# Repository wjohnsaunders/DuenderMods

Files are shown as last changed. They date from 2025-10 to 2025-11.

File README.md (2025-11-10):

# Modified files for Duender MGN9 Version

I wanted to use the updated MGN9 files for constructing my Duender. This
was because a number of improvements had been made to the design. Also I
I would like to install rails in the future without needing to reprint all
of the parts. The MGN9 has improved stacking of the flanged bearing using
0.5mm washers instead of printer shims.

I also saw the "Top Motor Mount w/ Double Shear for Duender" from Andizzle
on Printables, and liked how rigidly it mounted to the frame. However this
mount was not suitable for the MGN9 version.

These files are not re-mixes of the original STEP or STL files. I have
designed each one from scratch in FreeCAD using just the dimensions of
the original parts to make them work in place of the originals. However
I deem them a remix as they are intended for the Duender, and replace
the original parts in a like-for-like way.

I want to thank Sergei Irbis for the design of the Duender and providing
a means for my Ender 3 to continue as a useful 3D printer.

I also want to thank Andizzle for the improved motor mounts that I have
based my motor mounts design on.

## Front Tensions MGN9

This project contains a re-design of the front tensioner housings from
Sergei Irbis, and they re-use the stock pulley holder inserts.

The main change is that it uses the M5x45 and M5x25 bolts from the Ender
3 (you need to tap your threads into the extrusion at least 20mm) to make
for a very strong connection.

I have also adjusted the geometry to provide a solid end-stop for my newly
designed Wheel to MGN9 Adapters.

Finally I played with the asthetic to get something that I like better.

## Motor Mounts MGN9

This project contains a re-design of the motor mounts from Andizzle, however
adds 8mm to the deck height to make them compatible with the MGN9 project.

I also removed the trianguler mount from the bottom, as in the future I will
have a 20x40 extrusion there to support a 3rd heated bed mount. It seems
plenty strong enough without it.

Finally it uses the M5x45 bolts from the Ender 3 (you need to tap your
threads into the extrusion at least 20mm) to mount into the 2040 Y-axis
extrusions to make for a very strong connection.

You need to mount both of the motor mounts to 2020 extrusion first, as the
M5x45 bolts prevent access to the bolts that go into the end of the 2020
extrusion. Then you use the M5x45 bolts to mount the assembly to the frame.

Note that this redesign moves the bolt positions somewhat, so that you cannot
mix and match the top and bottom parts from Andizzles project. The belt path
remains compatible so there should not be any effect on kinematics.

## Wheel To MGN9 Adapter

This is the mod I first started working on. I was looking for options not
to have to buy a sheet of aluminium then drill and cut the plates. I used
purchased open-build plates for the Z axis, but this doesn't work for the
X gantry.

I noticed that the V-wheels posiion the plate approximately 4mm above the
top of the extrusion, where as an MGN9 carriage positions it 10mm above
the extrusion. It is known that the aluminium plates cannot be 3D printed
because 3mm thickness is not rigid enough.

So I thought that if I 3D printed a 6mm plate that should increase rigitity
and bring the alignment in line with an MGN9 carriage. So I decided I
would design a 6mm adapter than would look like an MGN9 carriage for the
stock parts to mount onto.

I have done a few revisions of this in order to move the inner wheel out of
the way of potential toolheads. I also had to move the rear outer wheel back
to provide stability against twisting. I believe it works well as a stop-gap
until you can install rails. The only negative is that you cannot adjust the
wheel tension without removing the stock parts from the top. So make sure
you adjust the wheel tension before full assembly.

## X Mount MGN12

This mod adds support for using an MGN12H linear rail and carriage for the X
axis.

I feel that these size rails mount better on the V-slot extrusions, and MGN12
is the current X axis standard for DIY printers like the Vorons and others.
It opens up more options for alternative toolheads and mounting systems. The
only con being that the nozzle is pushed further forward.

## EMS Panel and Various EMS Mounts

What is EMS? It is a system for managing the electronics for 3D printers from
FizzyTechs. It consists of a panel with hexagon cutouts, a set of hexagon
shaped plugs that fit into the panel, and a repository of mounts for various
3D printer electrical components. The idea is that if you replace a component,
or need to move one around, you can just print the mount for the new component,
or move the plugs to a different cutout. There are also plugs for zip-ties,
and a set of cable ducts for solving any cable management issue.

https://www.printables.com/model/558357-ft-ems-mounts-repository

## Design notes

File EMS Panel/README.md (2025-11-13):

# EMS Panel

This is an EMS panel for the Duender 3D printer. There is a version with
6 tabs and 8 tabs. The 8 tab option is useful if the Z steppers are
towards the middle, while the 8 tab option is better if the steppers are
further forward.

What is EMS? It is a system for managing the electronics for 3D printers
from FizzyTechs. It consists of a panel with hexagon cutouts, a set of
hexagon shaped plugs that fit into the panel, and a repository of mounts
for various 3D printer electrical components. The idea is that if you
replace a component, or need to move one around, you can just print the
mount for the new component, or move the plugs to a different cutout.
There are also plugs for zip-ties, and a set of cable ducts for solving
any cable management issue.

https://www.printables.com/model/558357-ft-ems-mounts-repository

Note that there is no upper lid for the electronics bay, I was thinking a sheet
of Acrylic with a cutout or two for fans. The hexagon holes in the EMS panel
will allow cooling air to pass out from underneath the Duender.

## Printing

Print with the flat side down, it should import in the correct orientation.
No supports are necessary. There are some bridges, but they should print OK
provided you have some part cooling enabled.

The model is 288x249 so you will need a printer capable of 300mm. You can
use the slicer to split it into 4 parts, then super glue it back together.
There are “dog-bone” joiners available for EMS if gluing is not strong enough.

The dimensions should give you 0.5mm gap all around, however filament
shrinkage could cause more gap. So it's best to calibrate the shrinkage for
your filament and set that in the slicer before printing.

## Installation

The panel mounts in the bottom of the rectangle formed by the 4040 extrusions
in the base of the Duender. Your electronics mounts to the base using the plugs
and adapter mounts from the FT EMS repository. I suggest working out the
electronics component placement while the EMS base is not installed, as it will
be easier to make adjustments. Once you have worked out the positions, remove
the components from the mounts, install the panel and re-install the components.

Use 8/6 sets of M5x8 bolt and M8 T-nut (should have a bunch available from the
corner braket packs) to bolt it to the upper V-slot. The EMS base should be
flush with the bottom of the 4040 extrusions, and should clear the Z-axis
steppers if you didn't use spacers to place them lower.

## CAD

The part is designed using FreeCAD.

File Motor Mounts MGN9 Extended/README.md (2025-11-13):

# Motor Mounts MGN9 Extended

This project takes my previous MGN9 Motor Mounts project and moves everything
further back to allow more Y axis travel. You will probably want to have 320mm
rails (get 350mm rails and trim 30mm from it with an Inox cutting wheel on an
angle grinder) with these mounts to give 280mm of Y travel (45mm outside the
print bed area).

Also the top half is relocated a further 10mm back, as I was having a problem
with the toolhead PCB (one that mounts to the extruder stepper) hitting the
top mounted stepper motors. The top half of the mounts are the same as my
previous mounts, so no need to reprint if you already have them.

Also note that you will need longer belts as a consequence of moving
everything back. Belt alignment stays the same, just the run from front to
back is longer.

You need to mount both of the motor mounts to 2020 extrusion first, as the
M5x45 (or M5x40) bolts prevent access to the bolts that go into the end of
the 2020 extrusion. Then you use the M5x45/40 bolts (4 instead of 2 in this
version) to mount the assembly to the frame.

## Printing

Print with the flat side down, it should import in the correct orientation.
The parts are designed such that no supports are required to print. I suggest
4 walls, 5 top and bottom layers, and 40% infill for strength as this part is
under tension from the belts. This is the standard Voron printing specs.

## Installation

You will need an M8 tap to cut a thread into the largest hole. This should
be easy as it is just plastic. I will try and figure out how to design a
thread so it gets 3D printed in a future revision.

Next you need 5 heat-set inserts per mount, M3x5x4, which go into the 5
middle sized holes. The circular end of the insert should fit into the
hole, then push it all the way in with a soldering iron.

Note: In order to get the insert properly aligned, I push it almost in,
then flip the part over and press down hard on a flat heat resistance
surface (I use a small sheet of aluminum on my desk). The remaining heat
allows the insert to go all the way in, and the flat surface ensures the
insert is properly aligned when the plastic sets hard.

Move your bearing stacks from the existing top cover to the new top cover.

Mount the top cover to the bottom part. The existing bolts should be OK,
6 x M3x30 and 1 x M8x35 (from Ender 3 Y-axis tensioner).

You will likely need to tap a longer M5 threads into the end of your Y
extrusions. I have designed for the M5x45 bolts to have 19mm of thread
protruding from the mount, so I suggest extending the thread length to
20mm with a tap. Or use the M5x40 bolts with a 15mm tapped hole. Make
sure to use the original thread to guide the tap in, as you don't want
it cutting a new thread that is out of alignment. Make sure to tap both
the top and bottom holes.

You will also need to tap a thread into the 2020 extrusion, the length
of the thread depends on the bolt length you use, but use a button head
bolt as there is no clearance for anything else. I would suggest an
M5x12 as a minimum, and an M5x16 is even better.

You then mount both of the motor mounts to 2020 extrusion first. Start
with a T-nut and M5x8 from the back of the mount, don't fully tighten.
Next install the M5x12/16 into the end of the 2020 extrusion, tighten
this first then go back and tighten the M5x8. Repeat for the motor
mount on the other side of the extrusion.

Finally use the M5x45/40 bolts to mount the rear-motor mount assembly
onto the frame. You might find that you need to flex the frame, if it
is slightly out of alignment, so that the bolts go in.

The rear of the frame should now be very rigid, and you should look at
adding a brace to the front of the frame to provide similar rigidity.

## CAD

The part is designed using FreeCAD.

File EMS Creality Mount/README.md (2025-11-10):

# EMS Creality Mount

This is an EMS mount for the Creality control boards as used in the older
Ender-3 and CR-10s.

What is EMS? It is a system for managing the electronics for 3D printers from
FizzyTechs. It consists of a panel with hexagon cutouts, a set of hexagon
shaped plugs that fit into the panel, and a repository of mounts for various
3D printer electrical components. The idea is that if you replace a component,
or need to move one around, you can just print the mount for the new component,
or move the plugs to a different cutout. There are also plugs for zip-ties,
and a set of cable ducts for solving any cable management issue.

https://www.printables.com/model/558357-ft-ems-mounts-repository

## Printing

Print with the flat side down, it should import in the correct orientation.
The part has been designed to print with no supports.

## Installation

Install 5 heatset inserts from the top. Attach the mount with some EMS plugs
into the base. Attach the Creality control board to the mount with some
M3x6 or M3x8 bolts.

## CAD

The part was designed using FreeCAD.

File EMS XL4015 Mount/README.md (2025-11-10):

# EMS XL4015 Mount

This is an EMS mount for the XL4015 voltage regular that is often used to
power Rasoberry Pis from a 3D printers 24V PSU.

What is EMS? It is a system for managing the electronics for 3D printers from
FizzyTechs. It consists of a panel with hexagon cutouts, a set of hexagon
shaped plugs that fit into the panel, and a repository of mounts for various
3D printer electrical components. The idea is that if you replace a component,
or need to move one around, you can just print the mount for the new component,
or move the plugs to a different cutout. There are also plugs for zip-ties,
and a set of cable ducts for solving any cable management issue.

https://www.printables.com/model/558357-ft-ems-mounts-repository

## Printing

Print with the flat side down, it should import in the correct orientation.
The part has been designed to print with no supports.

## Installation

Install 2 heatset inserts from the top. Attach the mount with an EMS plug or
two. Attach the XL4016 to the mount with some M3x6 or M3x8 bolts.

## CAD

The part was designed using FreeCAD.

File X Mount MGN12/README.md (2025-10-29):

# X Mount MGN12

This mod is for Duender MGN9, however it confusingly supports an MGN12 rail
on the X axis. Doing this expands the toolhead options as effectively any
Voron toolhead will simply fit as-is. I have a StealthBurner on mine, and
I used the Voron X Carriage STLs to mount it. However XOL, A4T, Archetype,
DragonBurner, etc will all simply bolt on. I would also like to experiment
with a StealthChanger for multiple heads in the future, and this mod
enables that. Some toolheads still support MGN9, but it is not as many as
supports MGN12.

Essentially all this mod does is move the idler pulley positions 3mm forward
to cater for the extra height in the MGN12 rail. I also fiddled with the
cutouts on the top to make it easy to get an allen wrench onto the bolt
underneath. This was a re-design in FreeCAD rather than an STL remix.

## Printing

Print with the flat side down, it should import in the correct orientation.
No supports are necessary. There are builtin bridges for the recessed holes,
so I suggest using a part cooling fan by the 3rd layer or so.

## Installation

After printing, install heat-set inserts in the left and right lower parts.

You will need 10 heat-set inserts in total, M3x5x4, installed as per the
original part. The circular end on the insert should fit into the hole, then
push it all the way in with a soldering iron. I recommend that they be
installed from bottom, as that provides a stronger connection. Note that for
the hole with the 10mm column, they can only go in from the bottom.

Note: In order to get the insert properly aligned, I push it almost in,
then flip the part over and press down hard on a flat heat resistance
surface. The remaining heat allows the insert to go all the way in, and
the flat surface ensures the insert is properly aligned and flush.

You will also need 10 x M3x30 bolts in total, along with bearings and shims.
All of the standard Duender MGN9 hardware fits in the equivalent locations.

Note: Shim stacks. In order to match the Voron belt spacing (4mm between the
inner edges of the belts) I have altered my bearing and shim stacks.
- On the stacks that have 2 bearing sets (the rear motor mounts) I use 1.5mm
of shims on the outside and 2mm of shims in the middle, and I don't use a shim
between the bearing halves because I don't want the belts moving up and down.
- On the stacks with a single bearing set, I use 1.5mm of shims on both sides.
Again no shims between the bearing halves.

## CAD

The part is designed using FreeCAD. I can't provide STEP files, sorry, as
FreeCAD can only import STEP files, it cannot export them as far as I know.

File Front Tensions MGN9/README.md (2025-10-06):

# Front Tensions MGN9

This project contains a re-design of the front tensioner housings from
Sergei Irbis, and they re-use the stock pulley holder inserts.

The main change is that it uses the M5x45 and M5x25 bolts from the Ender
3 (you need to tap your threads into the extrusion at least 20mm) to make
for a very strong connection.

I have also adjusted the geometry to provide a solid end-stop for my newly
designed Wheel to MGN9 Adapters.

Finally I played with the asthetic to get something that I like better.

## Printing

Print in the same orientation as the stock parts, it should import in the
correct orientation. No support is required as hole recesses have support
built into the model.

## Installation

These should pretty much be a swap from the original part, you re-use the
existing pulley holders so no rebuilding of the bearing stack.

However you will likely need to tap a longer M5 thread into the end of
your extrusions. I have designed for the M5x45 and M5x25 bolts to have
18mm of thread protruding from the mount, so I suggest extending the
thread length to 20mm with a tap.

Use some tape on the tap to make the 20mm position. Make sure to use the
original thread to guide the tap in, as you don't want it cutting a new
thread that is out of alignment.

## CAD

The part is designed using FreeCAD. I can't provide STEP files, sorry, as
FreeCAD can only import STEP files, it cannot export them as far as I know.

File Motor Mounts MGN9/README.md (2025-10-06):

# Motor Mounts MGN9

This project contains a re-design of the motor mounts from Andizzle, however
adds 8mm to the deck height to make them compatible with the MGN9 project.

I also removed the trianguler mount from the bottom, as in the future I will
have a 20x40 extrusion there to support a 3rd heated bed mount. It seems
plenty strong enough without it.

Finally it uses the M5x45 bolts from the Ender 3 (you need to tap your
threads into the extrusion at least 20mm) to mount into the 2040 Y-axis
extrusions to make for a very strong connection.

You need to mount both of the motor mounts to 2020 extrusion first, as the
M5x45 bolts prevent access to the bolts that go into the end of the 2020
extrusion. Then you use the M5x45 bolts to mount the assembly to the frame.

Note that this redesign moves the bolt positions somewhat, so that you cannot
mix and match the top and bottom parts from Andizzles project. The belt path
remains compatible so there should not be any effect on kinematics.

## Printing

Print with the flat side down, it should import in the correct orientation.
In order for the flange bearing recess to print correctlty, enable manual
supports, and paint the circular flange bearing recess in the slicer, and
when sliced check that support is generated just in that area.

I hope to produce a file with support designed in, but for now you will have
to use manual support and paint it on. Automatic support will work, however
it will fill the holes intended for the heatset inserts, and they are a
pain to remove.

## Installation

You will need an M8 tap to cut a thread into the largest hole. This should
be easy as it is just plastic. I will try and figure out how to design a
thread so it gets 3D printed in a future revision.

Next you need 5 heatset inserts per mount, M3x5x4, which go into the 5
middle sized holes. The circular end on the insert should fit into the
hole, then push it all the way in with a soldering iron.

Note: In order to get the insert properly aligned, I push it almost in,
then flip the part over and press down hard on a flat heat resistance
surface. The remaining heat alows the insert to go all the way in, and
the flat surface ensures the insert is properly aligned.

Move your bearing stacks from the existing top cover to the new top cover.

Mount the top cover to the bottom part. The existing bolts should be OK,
6 x M3x30 and 1 x M8x35 (from Ender 3 Y-axis tensioner).

You will likely need to tap a longer M5 thread into the end of your Y
extrusions. I have designed for the M5x45 bolts to have 18mm of thread
protruding from the mount, so I suggest extending the thread length to
20mm with a tap.

Use some tape on the tap to make the 20mm position. Make sure to use the
original thread to guide the tap in, as you don't want it cutting a new
thread that is out of alignment.

You will also need to tap a thread into the 2020 extrusion, the length
of the thread depends on the bolt length you use, but use a button head
bolt as there is no clearance for anything else. I would suggest an
M5x16 as a minimum to provide a strong connection.

You then mount both of the motor mounts to 2020 extrusion first. Start
with a T-nut and M5x8 from the back of the mount, don't fully tighten.
Next install the M5x16 into the end of the 2020 extrusion, tighten this
first then go back and tighten the M5x8. Repeat for the other motor
mount on the other side of the extrusion.

Finally use the M5x45 bolts to mount the rear-motor mount assembly onto
the frame. You might find that you need to flex the frame to line up
the bolts so that they go in.

The rear of the frame should now be very rigid, and you should look at
adding a brace to the front of the frame to provide similar rigitity.

## CAD

The part is designed using FreeCAD. I can't provide STEP files, sorry, as
FreeCAD can only import STEP files, it cannot export them as far as I know.

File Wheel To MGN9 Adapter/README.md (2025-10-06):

# Wheel To MGN9 Adapter

This is the mod I first started working on. I was looking for options not
to have to buy a sheet of aluminium then drill and cut the plates. I used
purchased open-build plates for the Z axis, but this doesn't work for the
X gantry.

I noticed that the V-wheels posiion the plate approximately 4mm above the
top of the extrusion, where as an MGN9 carriage positions it 10mm above
the extrusion. It is known that the aluminium plates cannot be 3D printed
because 3mm thickness is not rigid enough.

So I thought that if I 3D printed a 6mm plate that should increase rigitity
and bring the alignment in line with an MGN9 carriage. So I decided I
would design a 6mm adapter than would look like an MGN9 carriage for the
stock parts to mount onto.

I have done a few revisions of this in order to move the inner wheel out of
the way of potential toolheads. I also had to move the rear outer wheel back
to provide stability against twisting. I believe it works well as a stop-gap
until you can install rails. The only negative is that you cannot adjust the
wheel tension without removing the stock parts from the top. So make sure
you adjust the wheel tension before full assembly.

## Printing

Print with the flat side down, it should import in the correct orientation.
No supports are necessary.

## Installation

Install the heatset inserts before the wheels.

You will need 4 heatset inserts per adapter, M3x5x4, which go into the 4
inner holes. The circular end on the insert should fit into the hole, then
push it all the way in with a soldering iron. They can be installed from
either the top or bottom, but provide a stronger connection if they are
installed from underneath. You will need either M3x10 or M3x12 bolts to
attach the X axis parts to the adapter.

Note: In order to get the insert properly aligned, I push it almost in,
then flip the part over and press down hard on a flat heat resistance
surface. The remaining heat alows the insert to go all the way in, and
the flat surface ensures the insert is properly aligned.

Obtain 2 fixed position V-wheel assemblies, and 1 adjustable V-wheel assembly
from your box of Ender 3 parts (I used parts from the Z-axis).

The fixed wheels go on the outside, and the adjustable wheel on the inside.
Install a bolt, the bolt head should sit in the recess so that the top of
the adapter is flat. Put on either a spacer or the adjuster cam, then a
wheel and finally a bolt.

The fixed wheels can be tightened. Keep the adjustable wheel loose. Install
on the extrusion, adjust the cam until there is no slop, an you can still
turn the wheels with your fingers. The adapter should easilt slide back
and forth on the extrusion. Remove the adapter and do a final tighten.

They are now ready to install the stock X axis parts on top.

## CAD

The part is designed using FreeCAD. I can't provide STEP files, sorry, as
FreeCAD can only import STEP files, it cannot export them as far as I know.

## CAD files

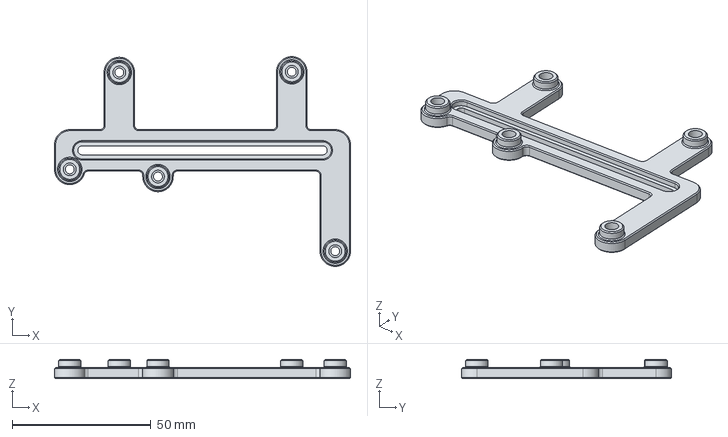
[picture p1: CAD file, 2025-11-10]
EMS Creality Mount/CAD/EMS Creality Mount.STEP
106.7 x 75.6 x 7.00 mm

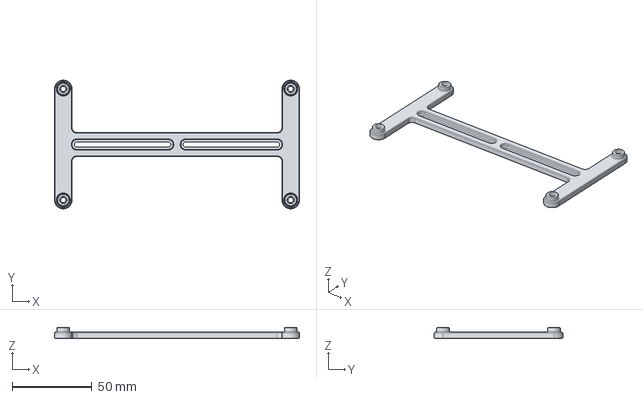
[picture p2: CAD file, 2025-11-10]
EMS Fysetc Spider Mount/CAD/EMS Fysetc Spider Mount.STEP
153.3 x 80.5 x 7.00 mm

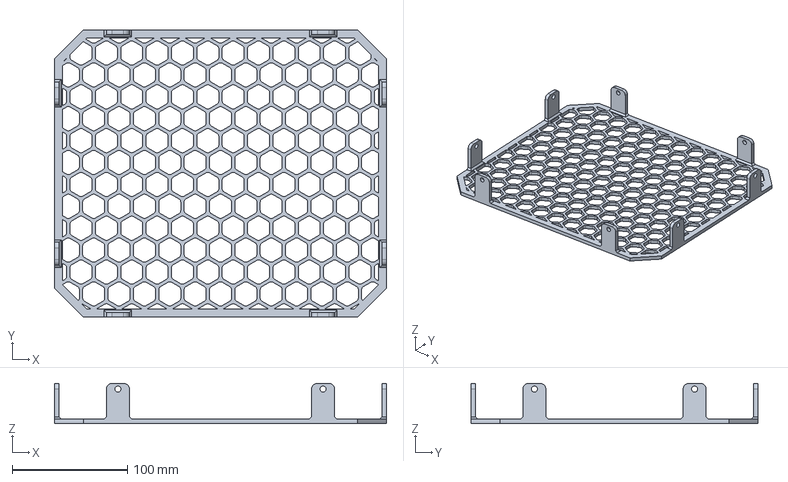
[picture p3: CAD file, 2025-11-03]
EMS Panel/CAD/EMS_Bottom.FCStd
288.0 x 249.0 x 35.0 mm

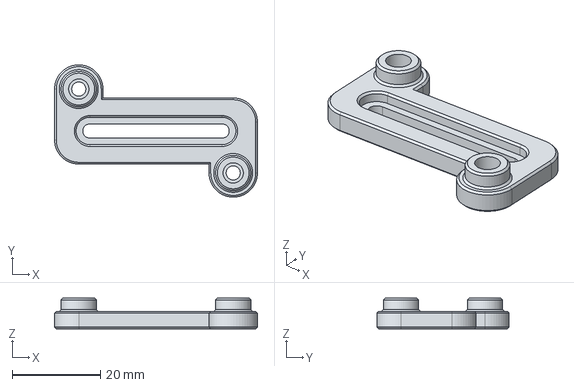
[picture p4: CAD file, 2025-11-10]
EMS XL4015 Mount/CAD/EMS XL4015 Mount.STEP
46.0 x 30.0 x 7.00 mm

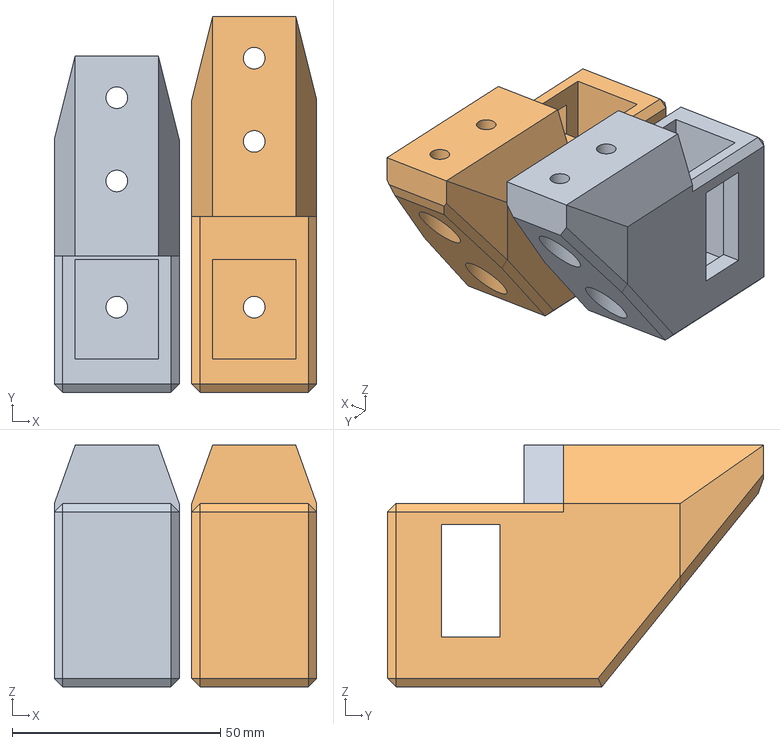
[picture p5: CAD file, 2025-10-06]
Front Tensions MGN9/CAD/FrontBeltTensioner.FCStd
63.0 x 90.3 x 58.0 mm
Left
Right

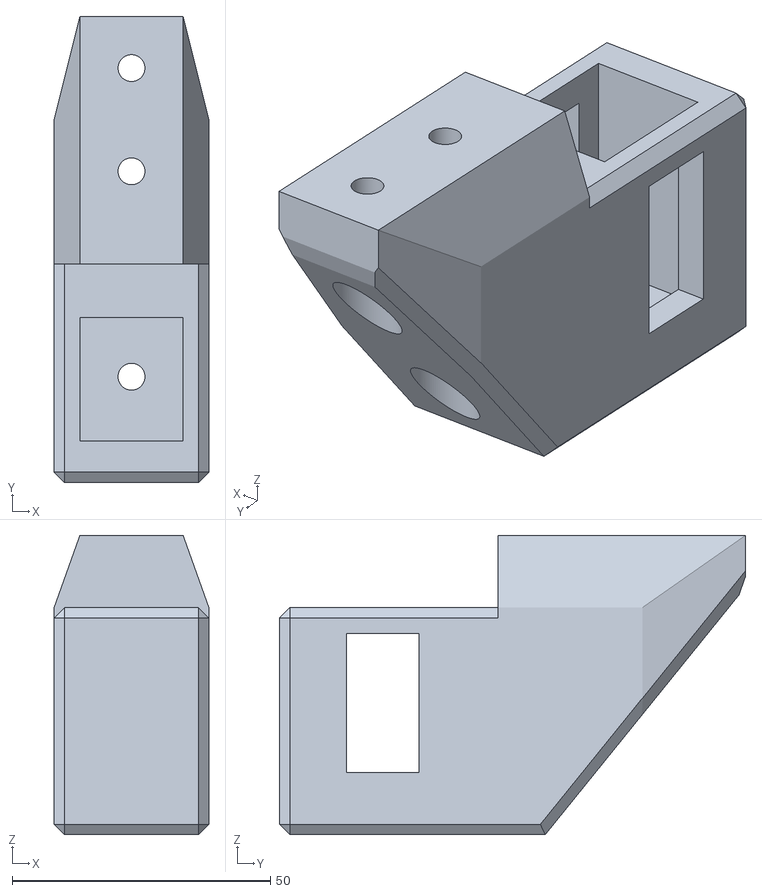
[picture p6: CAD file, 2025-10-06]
Front Tensions MGN9/STL/FrontBeltTensioner-Right.stl
30.0 x 90.3 x 58.0

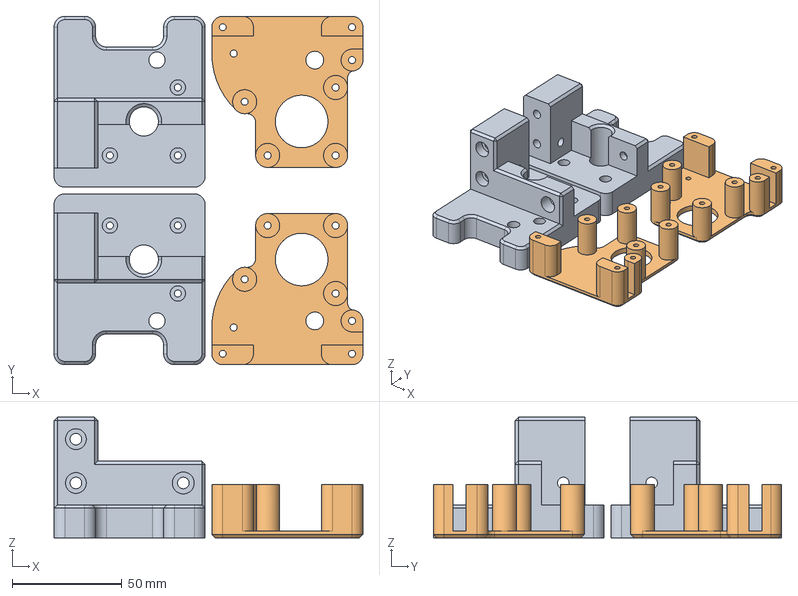
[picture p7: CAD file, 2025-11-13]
Motor Mounts MGN9 Extended/CAD/MotorMountMGN9Extended.step
141.0 x 159.0 x 55.0 mm
BottomRight
BottomLeft
TopRight
TopLeft

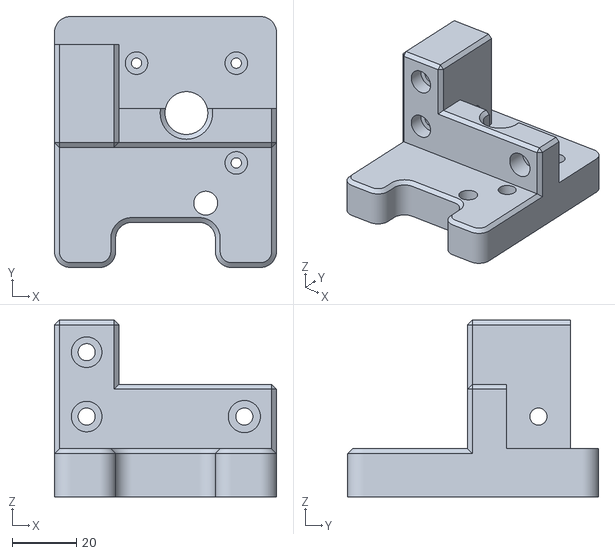
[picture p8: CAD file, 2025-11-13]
Motor Mounts MGN9 Extended/STL/MotorMountMGN9Extended-BottomLeft.stl
69.0 x 78.0 x 55.0

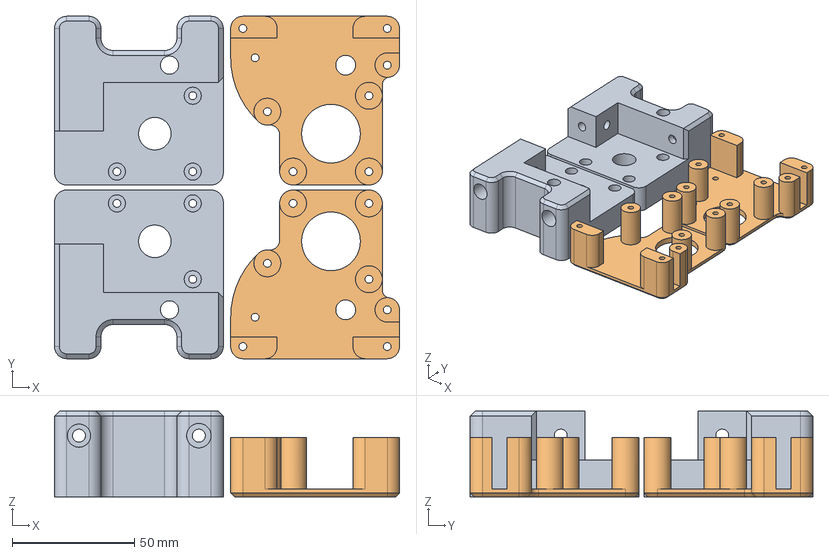
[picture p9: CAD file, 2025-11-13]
Motor Mounts MGN9/CAD/MotorMountMGN9.step
141.0 x 140.0 x 35.0 mm
BottomRight
BottomLeft
TopRight
TopLeft

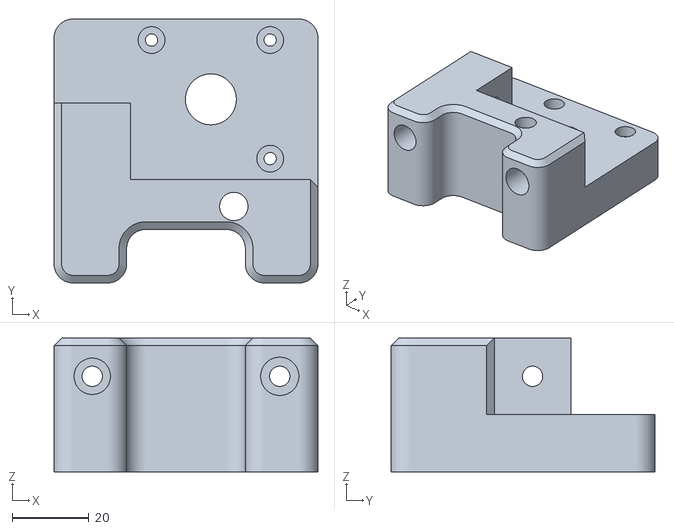
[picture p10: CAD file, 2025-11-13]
Motor Mounts MGN9/STL/MotorMountMGN9-BottomLeft.stl
69.0 x 69.0 x 35.0

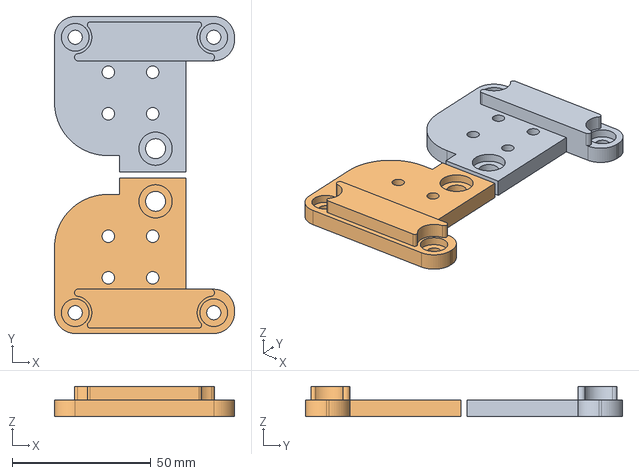
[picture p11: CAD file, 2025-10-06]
Wheel To MGN9 Adapter/CAD/WheelToMGN9Adapter.FCStd
65.0 x 114.4 x 11.0 mm
Left
Right

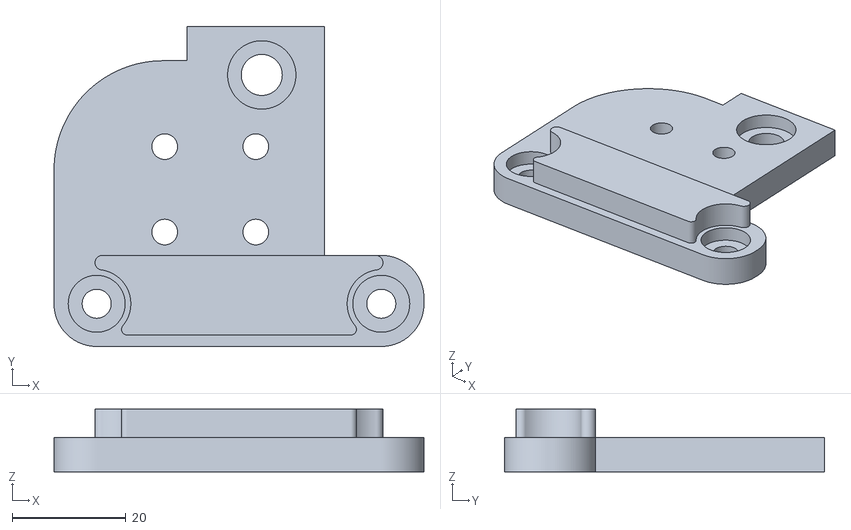
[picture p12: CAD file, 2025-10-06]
Wheel To MGN9 Adapter/STL/WheelToMGN9Adapter-Right.stl
65.0 x 56.2 x 11.0

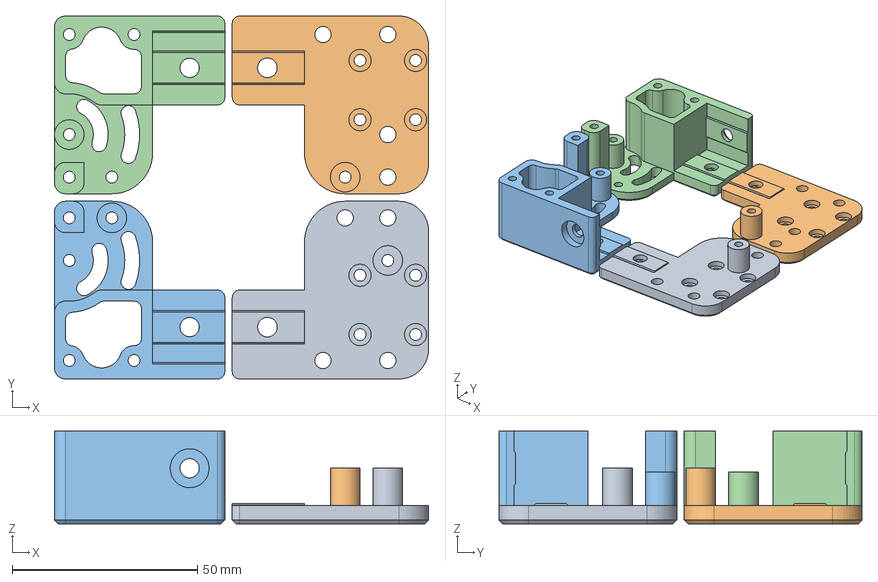
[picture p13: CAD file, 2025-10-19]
X Mount MGN12/CAD/X Mount MGN12.FCStd
101.0 x 98.0 x 25.0 mm
LeftLower
RightLower
LeftUpper
RightUpper

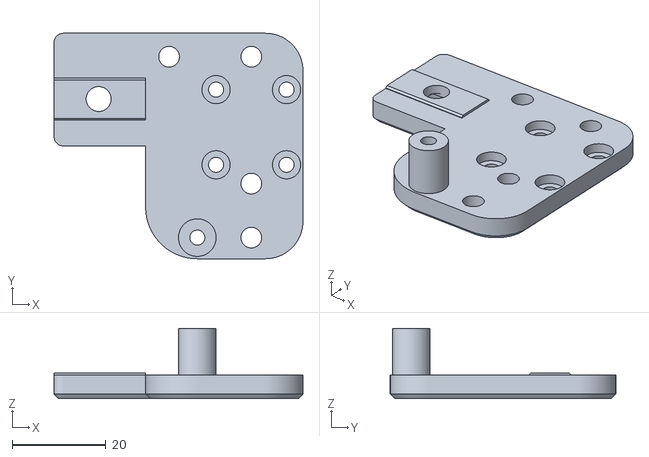
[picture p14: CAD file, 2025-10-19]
X Mount MGN12/STL/X Mount MGN12-RightLower.stl
53.0 x 48.0 x 15.0

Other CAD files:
EMS Fysetc Spider Mount/STL/EMS Fysetc Spider Mount-Body.stl
Front Tensions MGN9/STL/FrontBeltTensioner-Left.stl
Motor Mounts MGN9 Extended/STL/MotorMountMGN9Extended-BottomRight.stl
Motor Mounts MGN9/STL/MotorMountMGN9-BottomRight.stl
EMS Creality Mount/CAD/EMS Creality Mount.FCStd
EMS Fysetc Spider Mount/CAD/EMS Fysetc Spider Mount.FCStd
EMS XL4015 Mount/CAD/EMS XL4015 Mount.FCStd
Motor Mounts MGN9 Extended/CAD/MotorMountMGN9Extended.FCStd
Motor Mounts MGN9 Extended/STL/MotorMountMGN9Extended-TopLeft.stl
Motor Mounts MGN9 Extended/STL/MotorMountMGN9Extended-TopRight.stl
Motor Mounts MGN9/CAD/MotorMountMGN9.FCStd
Motor Mounts MGN9/STL/MotorMountMGN9-TopLeft.stl
Motor Mounts MGN9/STL/MotorMountMGN9-TopRight.stl
Wheel To MGN9 Adapter/STL/WheelToMGN9Adapter-Left.stl
X Mount MGN12/STL/X Mount MGN12-LeftLower.stl
X Mount MGN12/STL/X Mount MGN12-LeftUpper.stl
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

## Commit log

2025-10-06 Add initial set of designs
    [FrontBeltTensioner-Left.stl, FrontBeltTensioner-Right.stl, FrontBeltTensioner.FCStd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]
2025-10-11 Add chamfer to bottom motor mounts so it prints without supports
    [MotorMountMGN9-BottomLeft.stl, MotorMountMGN9-BottomRight.stl, MotorMountMGN9.FCStd]
2025-10-19 Add X Mount to support using an MGN12 for the X axis
    [X Mount MGN12.FCStd, X Mount MGN9-LeftLowerMGN12.stl, X Mount MGN9-LeftUpperMGN12.stl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]
2025-10-19 Add a chamfer so the lower X Mount MGN12 parts print without supports
    [X Mount MGN12-LeftLower.stl, X Mount MGN12-LeftUpper.stl, X Mount MGN12-RightLower.stl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]
2025-10-29 Add Duender EMS Panel
    [EMS_Bottom.FCStd]
2025-10-30 Add FT EMS Adapters for older Creality boards and the XL4015 regulator
    [EMS Creality Mount.FCStd, EMS XL4015 Mount.FCStd]
2025-10-30 XL4015 dimensions imported mirror image, fixed
    [EMS XL4015 Mount.FCStd]
2025-11-03 Resize the dimensions to give better fitment. Extend the tabs tso that they bolt to the upper V-slot which is easier to access.
    [EMS_Bottom.FCStd]
2025-11-10 Update EMS Creality mount so heatset inserts don't deform the plastic so much. Add a STEP file and fix the documentation.
    [EMS Creality Mount.FCStd, EMS Creality Mount.STEP]
2025-11-10 Add EMS mount for Fysetc Spider V3.0 and H7 boards that has heatset inserts.
    [EMS Fysetc Spider Mount-Body.stl, EMS Fysetc Spider Mount.FCStd, EMS Fysetc Spider Mount.STEP]
2025-11-10 Update XL4015 mount to use heatset inserts from the top. Updated README for several projects.
    [EMS XL4015 Mount.FCStd, EMS XL4015 Mount.STEP]
2025-11-13 Add extended motor mounts that allow 12mm more travel to the rea, and provided another 10mm clearance between the motor and the top rear of the toolhead.
    [MotorMountMGN9-BottomLeft.stl, MotorMountMGN9-BottomRight.stl, MotorMountMGN9.FCStd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]
2025-11-13 Cleanup some types and a wrong file commit
    [MotorMountMGN9Extended-BottomRight.step]
